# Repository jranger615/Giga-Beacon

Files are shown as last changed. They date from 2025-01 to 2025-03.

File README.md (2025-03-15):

### If inclined to send a tip for my hard work:
* Paypal: Jeff.b.ranger@gmail.com
* Venmo: @Jeff-Ranger-1

# Giga-Beacon
> [!IMPORTANT]
> <h2>This design requires the Beacon H - Normal Variant</h2>

> [!CAUTION]
> <i><b><H3>I am not responsible for any damage to your device, perform these modification at your own RISK!</H3></i></b>

https://github.com/user-attachments/assets/93804f33-2fc6-4fdc-bc21-9b3e94921d5a

<br />
<h2>Things to Consider</h2>
I highly recommend getting your Beacon from Lukes Lab so you can get the 5M USB for the Giga. (Make sure to notify them you want the Type H Normal Variant)
<br />https://www.lukeslabonline.com/products/beacon?variant=49920272597293

<h2>Refefrence Material</h2>
Beacon Install Quick Start Guide - This was used for reference in below configs
<br />https://docs.beacon3d.com/quickstart/ 

<h2>Things to Print</h2>
Download & Print <a href="https://github.com/jranger615/Giga-Beacon/blob/main/STL/Giga%20Beacon%20Adapter.stl">Giga Beacon Adapter.stl</a>
<br />You will need 6 m3x4 Heat Inserts. The LED Relocation bracket insers should installed from the bottom

<ul>
<li>ABS(Recommend)</li>
<li>.16 line height</li>
<li>3 Walls</li>
<li>4 Top/Bottom Layers</li>
</ul>

<h2>Hot End Modifications</h2>
<ul>
<li>Remove the Hot End from the Printer(4 M3 Screws, 2 front, 2 back)</li>
<li>Remove the Case by 2 M3 Screws attaching it</li>
<li>Remove the Pobe, 2 screws attach it to the metal casing, then trace the wire to the board and fish the wire out of the casing</li>
<li>Remove the 2 LED Screws and pull it to the side</li>
<li>Use a Dremel with Cut off Wheel to cut the metal casing as shows in the RED Outlines in the picture
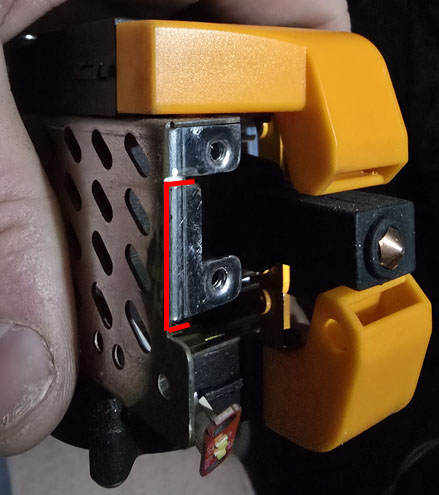
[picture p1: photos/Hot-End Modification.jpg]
<br />
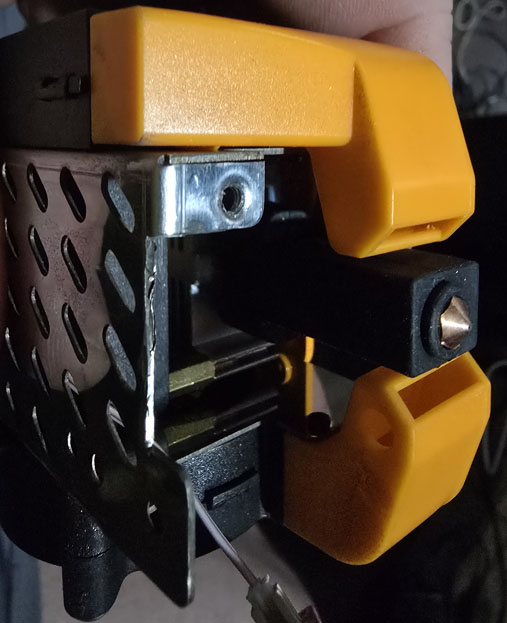
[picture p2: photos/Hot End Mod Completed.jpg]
</li>
<li>Using the cut off wheel Cut the Plastic Cover as shown in the picture
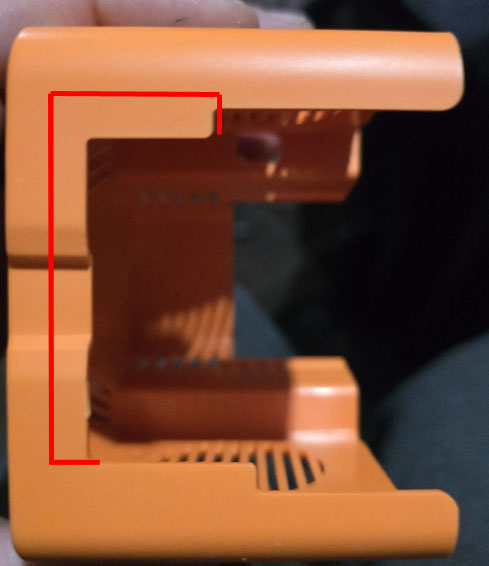
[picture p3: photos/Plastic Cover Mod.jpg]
<br /></li>
<li>Cut a hole in the top of the Plastic Casing big enough to fit the USB Cable End through, it can also be snaked through near the fan.
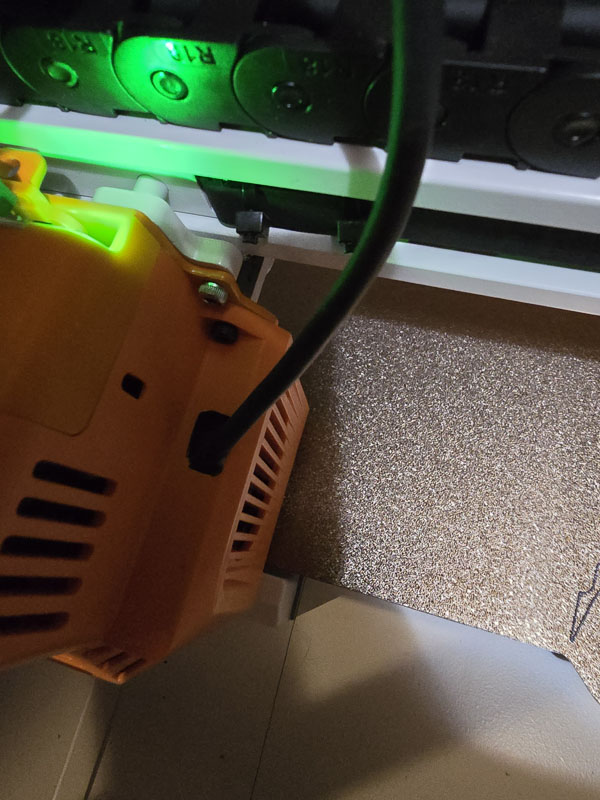
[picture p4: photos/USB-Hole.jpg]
<br /></li>
<li>Run the USB through the Cable Chains to the hot end location, fish it through the plastic cover, and down where the LED Use to be</li>
<li>Mount the USB on the Adapter with 2 M3 Screw</li>
<li>Mount the Adapter to the stock Sensor Location using 2 M3 Screw, make sure it is tight fitting against the side metal case near the LED. This helps make sure its flat</li>
<Li>Attach the USB to the Beacon, and secure the beacon to the Adapter with 2 M3 Screw
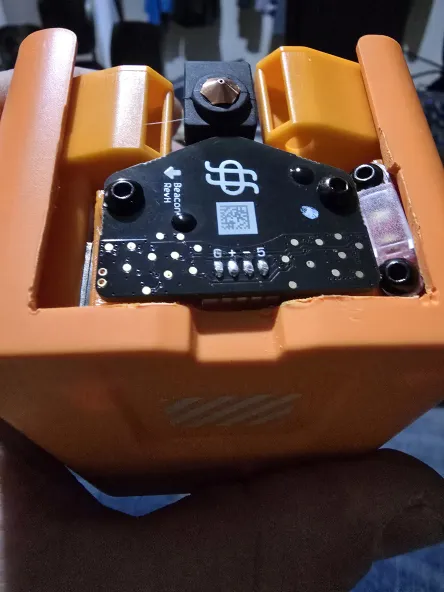
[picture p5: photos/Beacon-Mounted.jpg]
<br />
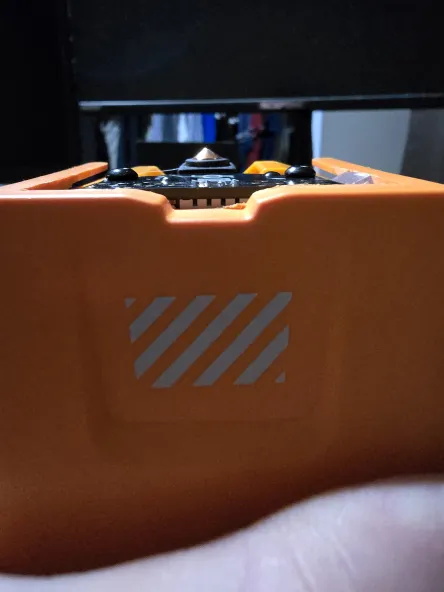
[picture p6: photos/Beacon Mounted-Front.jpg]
</Li>
<li>Re-Mount your Hot End to the Printer</li>
<li> PLug the USB into the Front Port on the Giga</li>
</ul>
<br />
<h2>Beacon Install/Configuration File Modifications</h2>

> [!IMPORTANT]
><b>Before you do this, turn on your printaer and HOME ALL.</b>

<ul>
<li>On your Klipper Screen, Click Settings > Advanced Settings > Root</li>
<li>Follow the Prompts to Root your Klipper and Allow SSH. Note the Username and PW</li>
<li>On your Pc Download Putty - https://www.putty.org/ </li>
<li>Open Putty and under Host Name type in the IP of your Giga. Should be on the right top corner of the Klipper Screen when connected to WIFI.</li>
<li>Click Connect, and log in with the supplied Credentials.   
<i><b><br />Username: Elegoo
<br />Password: giga3dp</li></i></b>
<li>Run these 3 commands 1 at a time, it will take some time to complete the Beacon Klipper Install.
  
  ```ruby
cd ~
git clone https://github.com/beacon3d/beacon_klipper.git
./beacon_klipper/install.sh
```
  
<li>Do not close putty, we will go back to this shortly</li>
<li>Navigate to Fluidd via your web browser using the IP from before</li>
<li>Choose the Configure Icon on the left, and click printer.cfg to started editing. (I recommend you backup this file to be safe before you begin)
<br />
</li>
<li> Comment Out the PROBE Section Completely with #. It Should look similar to this:
  
  ```ruby
#####################################################################
# 	Probe
 #####################################################################
#[probe]
#pin:^mcu1:gpio11
#x_offset: -14.0
#y_offset: -29.5
#z_offset: 0.0
#speed: 5.0
#samples: 2
#samples_result: median
#sample_retract_dist: 3.0
#samples_tolerance: 0.05
#samples_tolerance_retries:4</li></i></b>
```

<li>Add the following below the commented out Probe Section:
  
  ```ruby
[beacon]
serial: /dev/serial/by-id/usb-Beacon_Beacon_RevH_5BB811315157355957202020FF0E0F24-if00 #This will be REPLACED
x_offset: -1 # update with offset from nozzle on your machine
y_offset: -18 # update with offset from nozzle on your machine
mesh_main_direction: x
mesh_runs: 2
```

<li>Open Up Putty and Run the following Command
 <i><b><br />ls /dev/serial/by-id</li></i></b>
<li>Copy the USB line that contains Beacon, mine for example was <i><b>"usb-Beacon_Beacon_RevH_5BB811315157355957202020FF0E0F24-if00"</b></i></li>
<li>Paste the USB info in the beacon section under Serial:(It Should look like above but <i><b>/dev/serial/by-id/YOUR COPIED USB DATA HERE)</b></i></li>
<li>Find the section [stepper_z]</li>
<li>Comment Out with #:
 
  ```ruby
#endstop_pin:PC11
#position_endstop:0
 ```
  
   <li>Add the Following lines at the end of stepper_z
   
  ```ruby
endstop_pin: probe:z_virtual_endstop # use beacon as virtual endstop
homing_retract_dist: 0 # beacon needs this to be set to 0</i>
 ```

Under [stepper_z1] comment out with #:
  ```ruby
 #endstop_pin:PC10
 ```

<li>Add Under [stepper_z1] :
  
  ```ruby
  endstop_pin: probe:z_virtual_endstop # use beacon as virtual endstop
  ```

<li>Find the Safe_z_home section and make it as follows:
  
  ```ruby
  [safe_z_home]
home_xy_position: 405,205
# speed: 150
z_hop: 3          
#z_hop_speed: 5
  ```

<li> Click Save in the Top Right Corner, then close</li>
<li>Open moonraker.cfg</li>
<li>At the End Add the Following:

   ```ruby 
[update_manager beacon]
type: git_repo
channel: dev
path: ~/beacon_klipper
origin: https://github.com/beacon3d/beacon_klipper.git
env: ~/klippy-env/bin/python
requirements: requirements.txt
install_script: install.sh
is_system_service: False
managed_services: klipper
info_tags:
desc=Beacon Surface Scanner</i></b> </li>
   ```

<li> Click Save, and Close Again</li>
<Li>Run the following Command (Or Power off/on your Giga Again - This is usually most effective)
<br /><b><i>systemctl restart klipper</b></i></Li> 
<li>From Fluidd, chose the Command Icon</li>
<li><i><b>Run: G28 X Y</i></b></li>
<li><i><b>Run: G0 X605 Y205 to center it on Bed 1</i></b> </li> 
<i><b><li>Run: BEACON_CALIBRATE</i></b></li>
<li>You must now run commands and lower your Z like your setting the Z offset with the Supplied Metal Feeler or a Piece of Paper
<br /> The Command is :<i><b>TESTZ Z=-0.01</i></b>  (Lower it as little or increase it to move it down faster until it barely touches the Feeler or Piece  of Paper
<li>Once you have your Z Set, Remove the paper/feeler, and Run Command:  <i><b>ACCEPT</i></b> (It should state calibrating Beacon)</li>
<li> <i><b>Run Command: SAVE_CONFIG</i></b></li>
<Li>Now Heat the Primary BED your using and Re-Run the Beacon_calibrate Process</Li>
<li> Once Completed and You have ran Save_Config your can run a bed Calibration.
<br /> Command:  <i><b>BED_MESH_CALIBRATE</i></b> </li>
<h3> You’re now ready to print.</H3>
</ul>

> [!TIP]
>On the first print, you’ll want to use babystepping via the GUI to fine adjust the first layer offset.
>After the print finishes, the offset can be automatically applied to the model with the <b>Z_OFFSET_APPLY_PROBE</b> command for future prints.

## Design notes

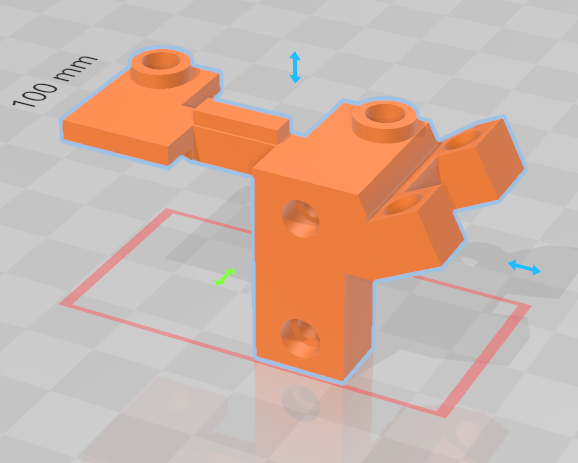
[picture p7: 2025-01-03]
photos/mount.jpg

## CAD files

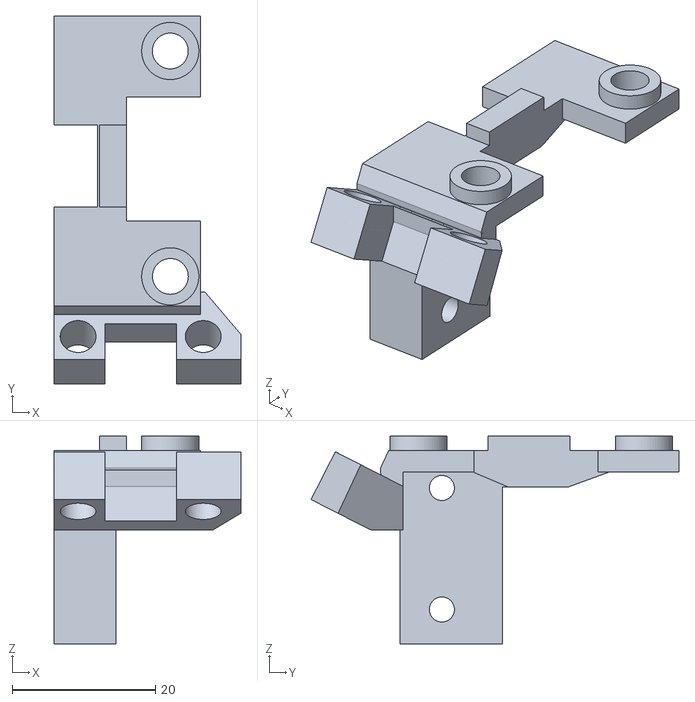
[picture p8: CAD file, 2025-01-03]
STL/Giga Beacon Adapter.stl
26.1 x 51.5 x 29.1

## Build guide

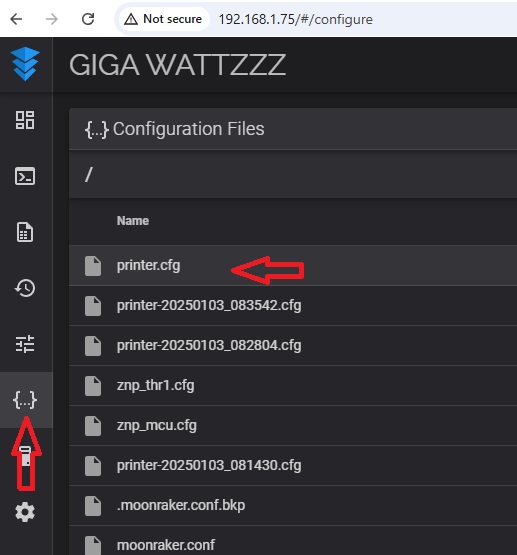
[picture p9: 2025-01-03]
photos/Configure-Printer.cfg.jpg

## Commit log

2025-01-03 Rename Giga Beacon Adapter.stl to STL/Giga Beacon Adapter.stl
    [Giga Beacon Adapter.stl]
2025-01-03 Rename Beacon Mounted-Front.jpg to photos/Beacon Mounted-Front.jpg
